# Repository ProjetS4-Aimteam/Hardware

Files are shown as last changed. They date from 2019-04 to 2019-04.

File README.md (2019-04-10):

# Hardware
Repository containing everything needed to build the Aim-Bot

***************************************************************************
Repo presented by the Aim-Team
from Univesité de Sherbrooke
Winter 2019

Carl-Philippe Cyr Mercier - cyrc2702@usherbrooke.ca
Simon Therrien - thes2210@usherbrooke.ca
Francis Roy - royf2112@usherbrooke.ca
Olivier Julien - julo2201@usherbrooke.ca
Marie Lepage - lepm3403@usherbrooke.ca

****************************************************************************
Whoaa there is a lot of files!!! 
Don't be afraid. We're here to guide you building your Aim-bot. Here are some informations you will need to get started.
****************************************************************************

First, you have to be aware of the need to make some 3D printing, and some laser cutting. Annnnnd for the latest version even some drilling and gluing! If you are not equipped for it, we will refer you to www.google.com, a great website where you can find many many people willing to help you make your parts for some $$$$.

*****************************************************************************
What you will use in this repository: everything, but here's how.
*****************************************************************************

 - First, there is a .PDF file to show you what the robot will look like once built. The name of this file is master_assembly.pdf. You may want to open it with Adobe acrobat reader DC because the 3D pdf seems to cause problems directly on the internet browser. In mine it does...
 
 - The BoM.xls file give a good feel of how much parts there is. It also shows you how we built the homemade (3D printed or laser cut)      parts, the material and the quatity of each. For the parts that are to buy (motors, OpenCR card, RPI, and also some standard ones),        the link of a website to buy them is given. You should know that there are plenty of other sites to buy it and this is only suggestions.

 - To facilitate your life, two folders "fab/dxf" and "fab/stl" are given with the parts exported from solidworks in extensions used for 3D printing (stl) and laser cutting (dxf).
 
 - When its time for assembling, some plans may be nice. We got exploded views of each assembly, leading to the complete build.
 those are the files named " master_assembly.pdf" and  "launcher_assembly.pdf"
 
*****************************************************************************
For modification / amelioration of the model
*****************************************************************************

 - The master_assembly.SLDASM file links every solidworks files, you may use it for modification of the original design.

 - The solidworks version used to draw the robot is 2018, you will have problem opening the parts if you want to modify them with an older version.

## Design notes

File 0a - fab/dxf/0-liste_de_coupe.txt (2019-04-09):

materiel: ABS 6 mm
Note: lors de la coupe le coté ruff doit etre vers le haut.

roue 2x
main_plate 1x
base_plate 1x
base_top
plaque_de_base 1x
base_side_r 1x
base_side_l 1x
base_front 1x
base_back 1x

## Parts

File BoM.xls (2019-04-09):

No. ARTICLE | NUMERO DE PIECE | DESCRIPTION | Source | QTE
1 | launcher_main_plate | MATERIAL: PLA | PRINTED | 1
2 | launcher_ball_guide | MATERIAL: PLA | PRINTED | 1
3 | RB-Hit-48 | Hitec HS-311 Servo Motor | https://www.robotshop.com/uk/hitec-hs-311-servo- motor.html?gclid=EAIaIQobChMI4vGErNHD4QIVSAOGCh1XLATl EAAYASAAEgLXifD_BwE | 1
4 | launcher_feeder_guid e | MATERIAL: PLA | PRINTED | 1
5 | launcher_feeder | MATERIAL: PLA | PRINTED | 1
6 | launcher_ball_tank | MATERIAL: PLA | PRINTED | 1
7 | launcher_wheel | MATERIAL: ABS 6MM | LASER_CUT | 2
8 | launcher_ball | PING PONG BALL | WALMART | 1
9 | launcher_base_plate | MATERIAL: ABS 6MM | LASER_CUT | 1
10 | XL430-W250-T | DYNAMIXEL | https://www.robotshop.com/en/xl430-w250-t-dynamixel-smart- servo- motor.html?gclid=EAIaIQobChMI2Mik9qvB4QIVE1qGCh3FnwjLE AAYASAAEgJiDvD_BwE | 2
11 | gear-m20-20t | MATERIAL: PLA | PRINTED | 1
12 | big gear-m20-82t | MATERIAL: PLA | PRINTED | 1
13 | 25d-metal-gearmotor- 75-99 | 9.7:1 Metal Gearmotor 25Dx48L mm HP 12V with 48 CPR Encoder | https://www.pololu.com/product/3214 | 1
14 | coupling_hex_12mm |  |  | 1
15 | pololu_DC_motor_hold er | MATERIAL: PLA | PRINTED | 1
16 | spur gear_14t_hex_v2 | MATERIAL: PLA | PRINTED | 1
17 | spur gear_14t_hub_v2 | MATERIAL: PLA | PRINTED | 1
18 | gear_drive_guard | MATERIAL: PLA | PRINTED | 1
19 | gear_tilt_guard | MATERIAL: PLA | PRINTED | 1
20 | 545548 | 0.770" Pattern Set Screw Hubs | https://www.servocity.com/770-set-screw-hubs | 3
21 | 545444 | dual_ball_bearing_hub | https://www.servocity.com/dual-ball-bearing-hub | 6
22 | 585424 | 90deg Single Angle Pattern Bracket | https://www.servocity.com/90-single-angle-channel-bracket | 2
23 | 615398 | 1/4" Bore Shaft Mount Bevel Gears | https://www.servocity.com/250-bore-bevel-gears | 4
24 | 634068 | 1/4" Stainless Steel D-Shafting - 2'' | https://www.servocity.com/0-250-1-4-stainless-steel-d-shafting | 2
25 | 634084 | 1/4" Stainless Steel D-Shafting - 6'' | https://www.servocity.com/0-250-1-4-stainless-steel-d-shafting | 3
26 | spacers_633104 | .250" Bore x .0625" Thick Black Delrin Spacer (12pk) | https://www.robotshop.com/media/files/pdf/actobotics- assortment-pack-Includes.pdf | 2
27 | 585532 | 90deg Angle Bracket | https://www.servocity.com/90-angle-bracket-a | 4
28 | 585584 | Flat 0.770" Pattern Bracket B | https://www.servocity.com/flat-bracket-b | 2
29 | 585422 | Flat Dual Pattern Bracket | https://www.servocity.com/flat-dual-channel-bracket | 2
30 | 585542 | 1/4" Bore Bottom Tapped Clamping Mount | https://www.servocity.com/1-4-bottom-tapped-clamping- mount | 2
31 | 633140 | 6-32 Thread, 1/4" OD Round Aluminum Standoffs , 1.5'' | https://www.servocity.com/6-32-thread-1-4-od-round- aluminum-standoffs | 2
32 | 585506 | 90° Single Angle Short Pattern Bracket | https://www.servocity.com/90-single-angle-short-channel- bracket | 1
33 | 585468 | Flat Single Pattern Bracket | https://www.servocity.com/flat-single-channel-bracket | 1
34 | 545360 | Side Tapped Pattern Mount C | https://www.servocity.com/90-quad-hub-mount-c | 2
36 | KINECT XBOX | WE GOT A USED KINECT BUT THERE ARE NEW ONES: | https://www.amazon.ca/gp/offer- listing/B002BSA298/ref=dp_olp_new?ie=UTF8&condition=new | 1
37 | Raspi3B+_Mock | Raspberri py starter kit | https://www.canakit.com/raspberry-pi-3-model-b-plus-starter- kit.html | 1
38 | STM32F746ZGT6 | Contrôleur Dynamixel OpenCR 1.0 | http://emanual.robotis.com/docs/en/parts/controller/opencr10 / | 1
39 | motor drive | Contrôleur de Moteur DC 13A Cytron | Contrôleur de Moteur DC 13A Cytron | 1
40 | bearing 7x8x22 | BC Precision 8BC608ZZ Eight (8) 608ZZ 8x22x7 Shielded Greased Miniature Ball Bearings | https://www.amazon.ca/BC-Precision-8BC608ZZ-Shielded- Miniature/dp/B00NX23HGQ/ref=sr_1_1?keywords=bearing+7x8x 22&qid=1554835239&s=gateway&sr=8-1 | 4
41 | 91290A426 | Black-Oxide Alloy Steel Socket Head Screw, M8 x 1.25 mm Thread, 20 mm Long | https://www.mcmaster.com/catalog/125/3205 | 4
42 | master_base_plate | MATERIAL: ABS 6MM | LASER_CUT | 1
43 | master_base_back | MATERIAL: ABS 6MM | LASER_CUT | 1
44 | master_base_side | MATERIAL: ABS 6MM | LASER_CUT | 2
45 | master_base_front | MATERIAL: ABS 6MM | LASER_CUT | 1
46 | master_base_top | MATERIAL: ABS 6MM | LASER_CUT | 1
47 | master_coupling_pan | MATERIAL: PLA | PRINTED | 1
48 | 40x40x10 DC Fan | DC cooling fan | https://www.amazon.com/Dc-Fan-40x40x10-Mm- 12v/dp/B00EXWNJEU | 2

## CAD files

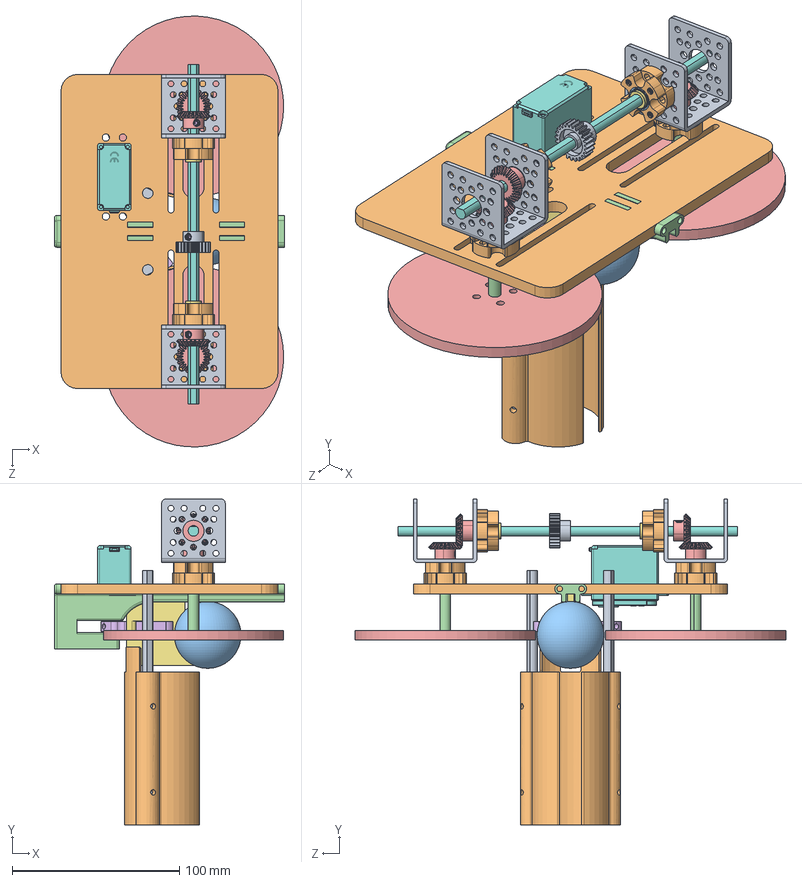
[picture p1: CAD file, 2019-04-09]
transmission.SLDASM
138.0 x 195.2 x 257.9 mm
bracket_585440-2 x 2
545444.STEP x 4
535020.STEP x 8
2_inch_shaft x 2
615398.STEP x 4
632134_91375A436.STEP x 5
spacers_633104 x 2
8_inch_shaft
615266_Gear Blank.STEP
Pièce1^transmission
balle
Pièce4^transmission
roue x 2
Pivot1Poussoir
Poussoir^transmission
Hitec Servo Motor HS-311
Pièce3^transmission x 2
Pièce6^transmission

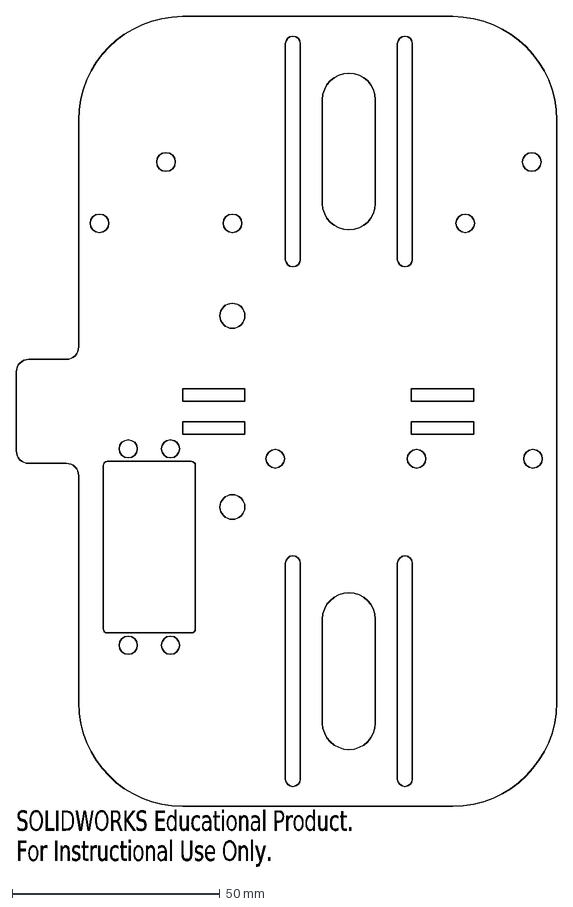
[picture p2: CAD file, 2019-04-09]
0a - fab/dxf/main_plate.DXF
SOLIDWORKS Educational Product.
For Instructional Use Only.

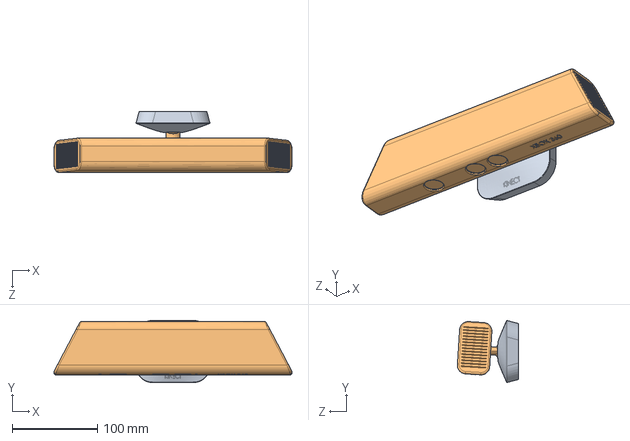
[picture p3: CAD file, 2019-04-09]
Kinect.SLDASM
279.4 x 72.8 x 71.8 mm
base KINECT
KINECT XBOX

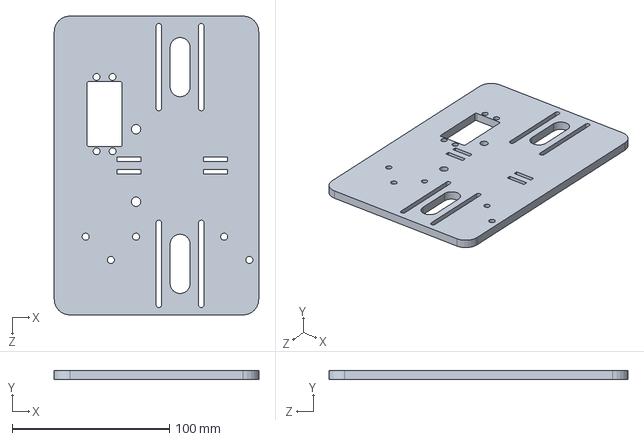
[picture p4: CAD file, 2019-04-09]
launcher_main_plate.sldprt
130.0 x 6.00 x 190.0 mm

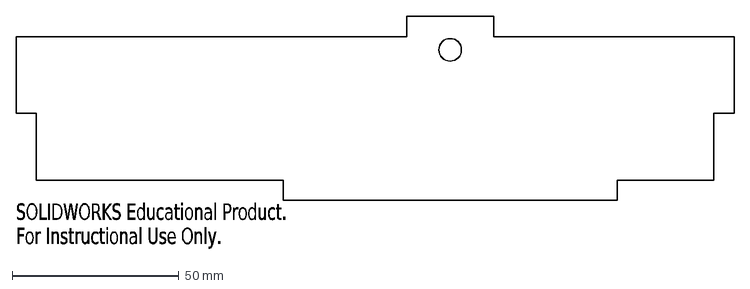
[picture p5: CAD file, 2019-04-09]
0a - fab/dxf/base_side_l.DXF
SOLIDWORKS Educational Product.
For Instructional Use Only.

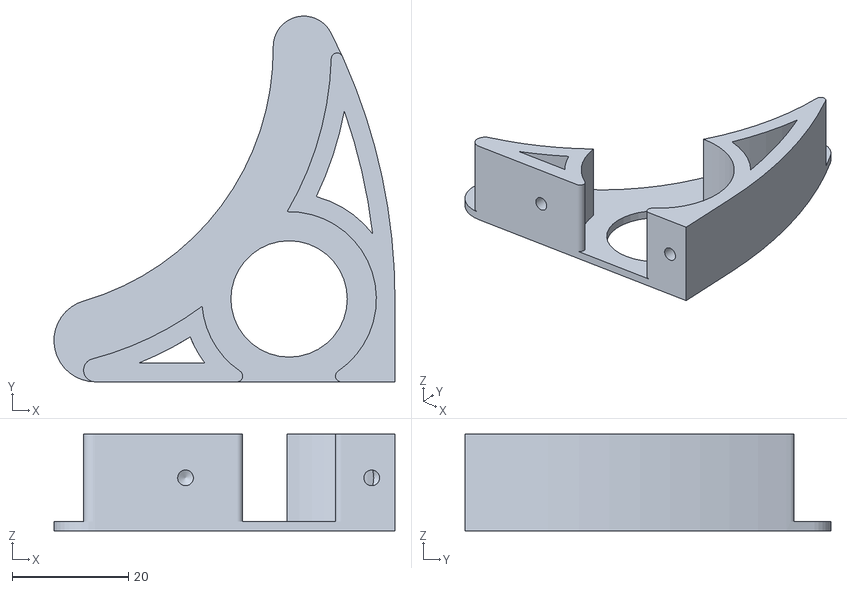
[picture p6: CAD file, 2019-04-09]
0a - fab/stl/garde_gear_tilt.STL
58.6 x 62.8 x 16.6

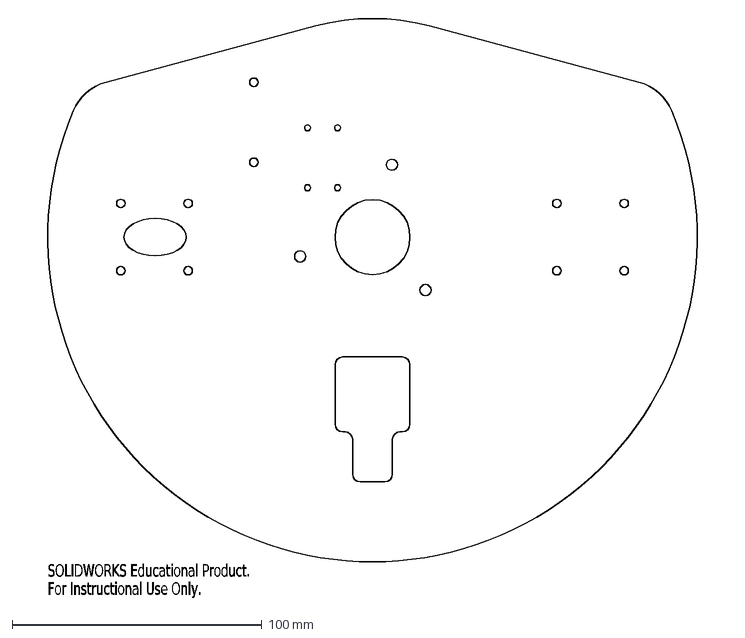
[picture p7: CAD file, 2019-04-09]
0a - fab/dxf/base_plate.DXF
SOLIDWORKS Educational Product.
For Instructional Use Only.

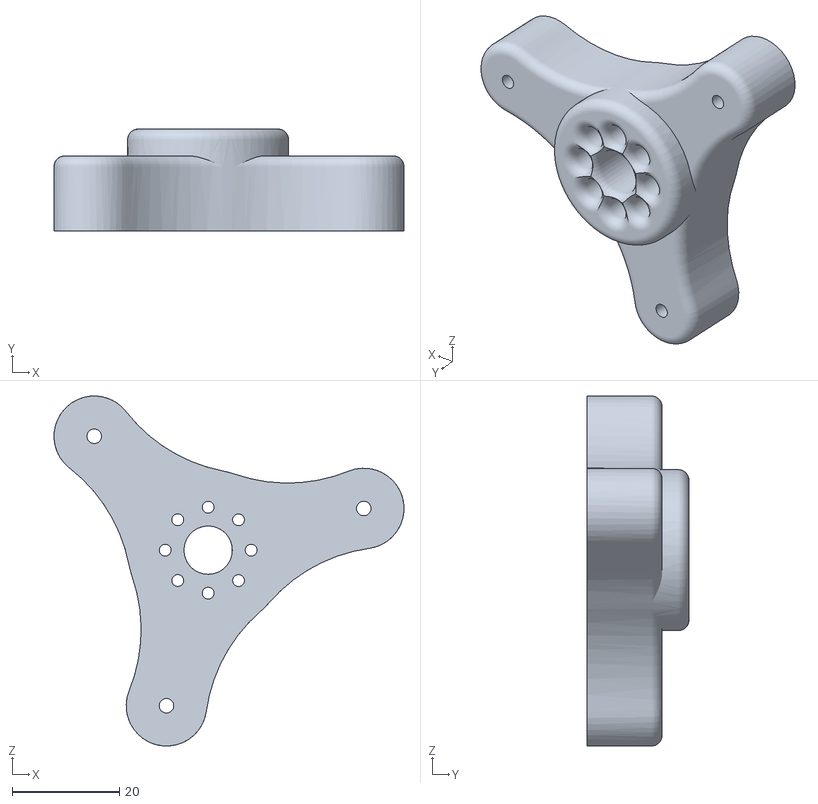
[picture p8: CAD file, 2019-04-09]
0a - fab/stl/coupling_pan.STL
65.2 x 19.0 x 65.2

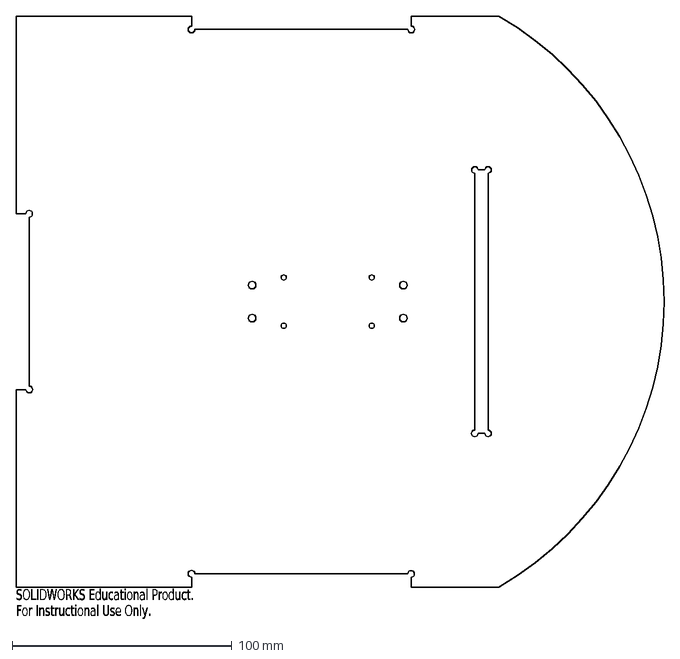
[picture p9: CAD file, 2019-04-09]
0a - fab/dxf/Plaque_de_base.DXF
SOLIDWORKS Educational Product.
For Instructional Use Only.

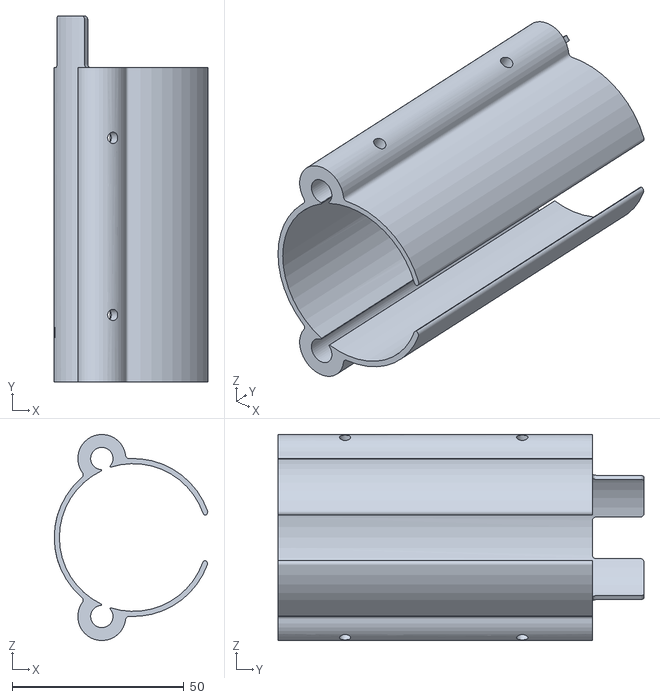
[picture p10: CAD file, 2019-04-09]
0a - fab/stl/resevoir_balles.STL
44.7 x 106.5 x 60.0

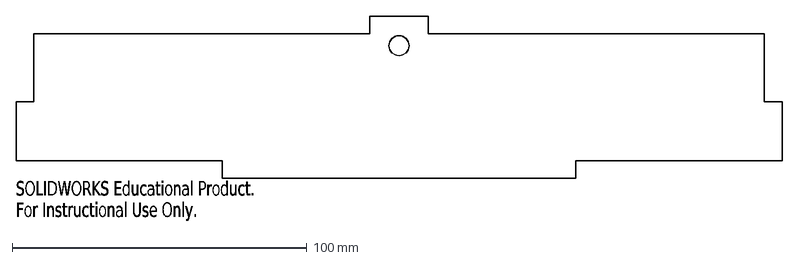
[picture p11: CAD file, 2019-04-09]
0a - fab/dxf/base_front.DXF
SOLIDWORKS Educational Product.
For Instructional Use Only.

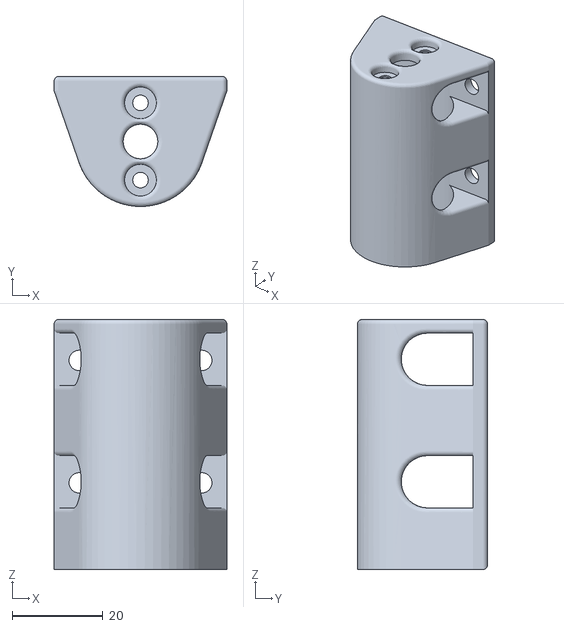
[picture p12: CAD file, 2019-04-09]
0a - fab/stl/petite-200-003-support_moteur-v9.STL
38.0 x 28.6 x 55.0

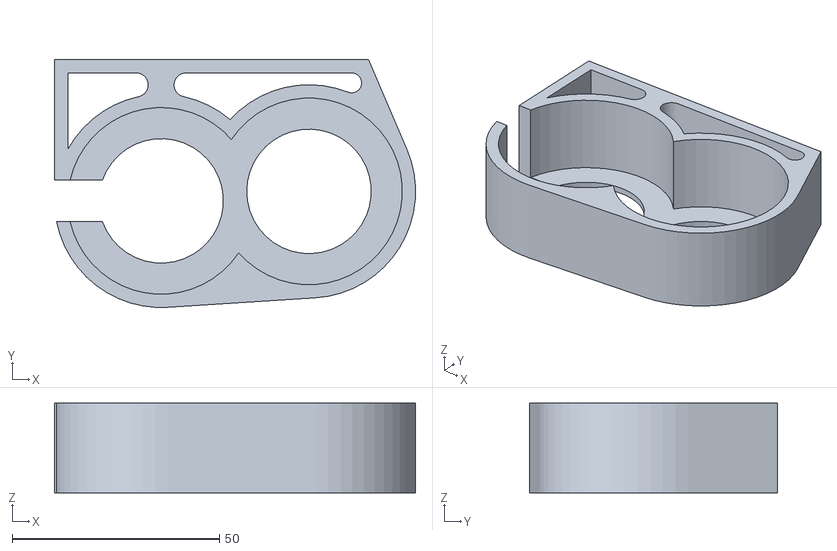
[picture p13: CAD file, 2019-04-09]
0a - fab/stl/garde_gear_drive.STL
87.0 x 59.7 x 21.6

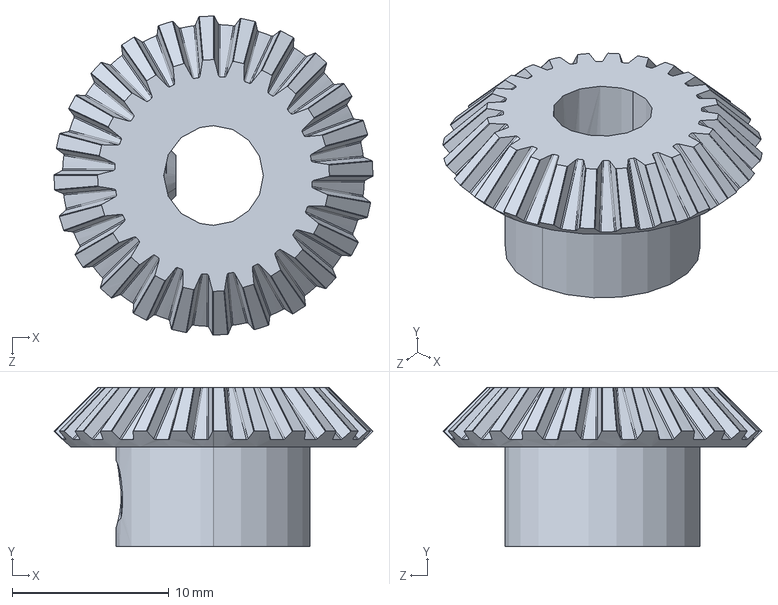
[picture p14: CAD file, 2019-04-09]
bore_shaft_bevel_gear_615398.SLDPRT
20.3 x 10.1 x 20.3 mm

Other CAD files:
master_base_back.sldprt
0a - fab/dxf/roue.DXF
0a - fab/stl/spur gear_14t_hex_v2.STL
0a - fab/dxf/base_back.DXF
0a - fab/dxf/base_side_r.DXF
0a - fab/dxf/base_top.DXF
0a - fab/stl/Poussoir.STL
0a - fab/stl/big gear-m20-82t.STL
0a - fab/stl/gear-m20-20t.STL
0a - fab/stl/guide.STL
0a - fab/stl/spur gear_14t_hub_v2.STL
0a - fab/stl/support_moteur_pan.STL
25d-metal-gearmotor-75-99.SLDPRT
2_inch_shaft.SLDPRT
40x40x10 DC Fan.SLDPRT
545360.SLDPRT
545548 assembly.SLDPRT
585422.SLDPRT
585424.SLDPRT
585468.SLDPRT
585506.SLDPRT
585532.SLDPRT
585542 .SLDPRT
585584.SLDPRT
633140.SLDPRT
6_inch_shaft.SLDPRT
91290A426_BLACK-OXIDE CLASS 12.9 SOCKET HEAD CAP SCREW.SLDPRT
DXL X430 .SLDPRT
Hitec Servo Motor HS-311.SLDPRT
KINECT XBOX.SLDPRT
Raspi3B+_Mock.SLDPRT
base KINECT.SLDPRT
bearing 7x8x22.SLDPRT
big gear-m20-82t.SLDPRT
coupling_hex_12mm.SLDPRT
dual_ball_bearing_hub_545444.SLDPRT
gear-m20-20t.SLDPRT
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

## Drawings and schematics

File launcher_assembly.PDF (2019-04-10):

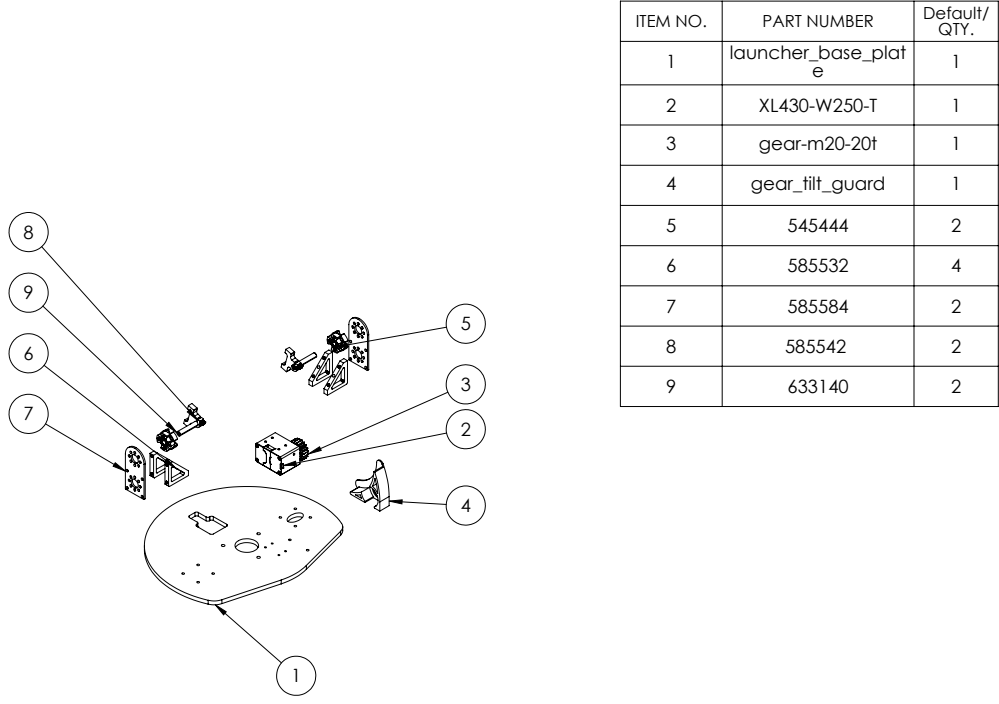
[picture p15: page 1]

ITEM NO. | PART NUMBER | Default/ QTY.
1 | launcher_base_plat e | 1

2 | XL430-W250-T | 1
3 | gear-m20-20t | 1
4 | gear_tilt_guard | 1
5 | 545444 | 2
6 | 585532 | 4
7 | 585584 | 2
8 | 585542 | 2
9 | 633140 | 2

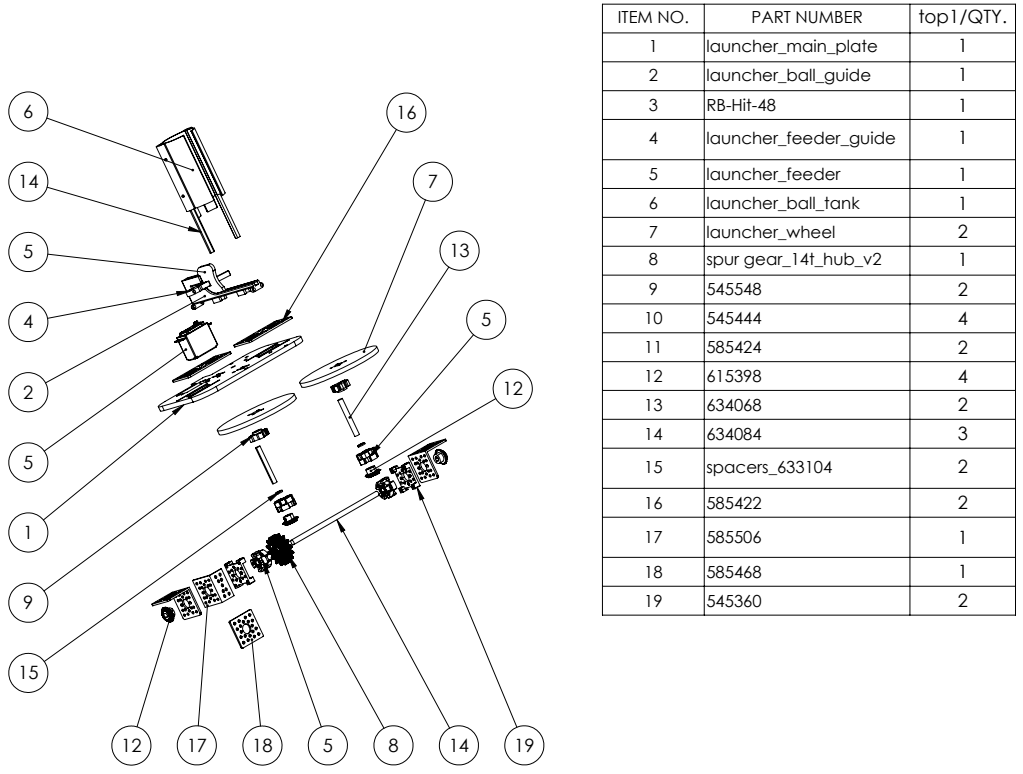
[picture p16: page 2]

ITEM NO. | PART NUMBER | top1/QTY.
1 | launcher_main_plate | 1
2 | launcher_ball_guide | 1
3 | RB-Hit-48 | 1
4 | launcher_feeder_guide | 1
5 | launcher_feeder | 1
6 | launcher_ball_tank | 1
7 | launcher_wheel | 2
8 | spur gear_14t_hub_v2 | 1
9 | 545548 | 2
10 | 545444 | 4
11 | 585424 | 2
12 | 615398 | 4
13 | 634068 | 2
14 | 634084 | 3
15 | spacers_633104 | 2
16 | 585422 | 2
17 | 585506 | 1
18 | 585468 | 1
19 | 545360 | 2

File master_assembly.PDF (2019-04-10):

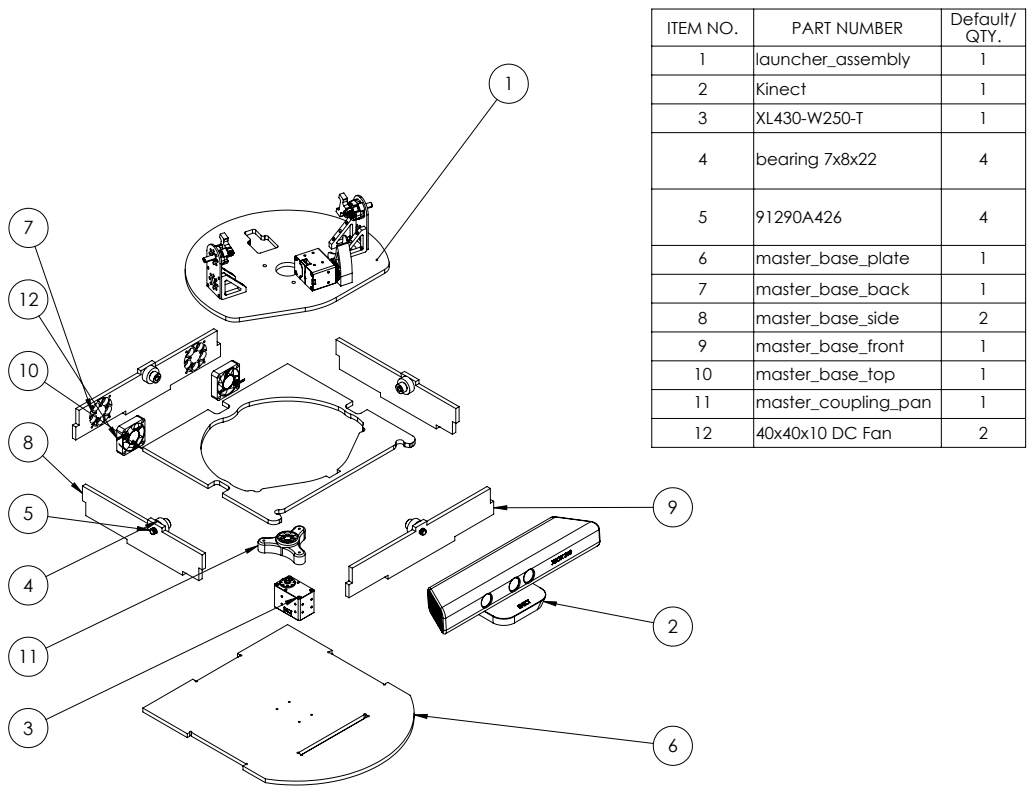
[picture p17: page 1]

ITEM NO. | PART NUMBER | Default/ QTY.
1 | launcher_assembly | 1
2 | Kinect | 1
3 | XL430-W250-T | 1
4 | bearing 7x8x22 | 4

5 | 91290A426 | 4
6 | master_base_plate | 1
7 | master_base_back | 1
8 | master_base_side | 2
9 | master_base_front | 1
10 | master_base_top | 1
11 | master_coupling_pan | 1
12 | 40x40x10 DC Fan | 2
